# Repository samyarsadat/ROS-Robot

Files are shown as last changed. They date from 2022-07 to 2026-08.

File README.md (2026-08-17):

<h1 align="center">The ROS Robot Project</h1>

<br>

<p align="center">
	
	<br>
	<br>
	
	|
	
	|
	
</p>

<br>

----
> [!NOTE]
> This project was completed and effectively reached its objective in September 2025.\
> There will be no further development. I have moved my focus to the 2nd revision of The ROS Robot.

<br>

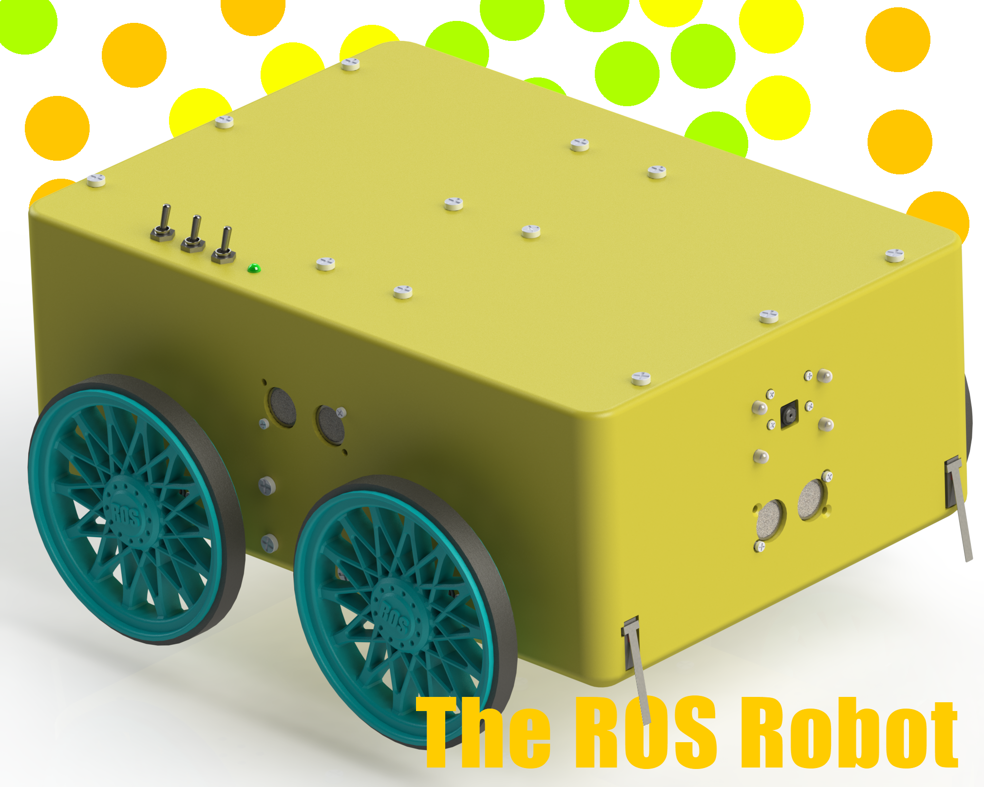
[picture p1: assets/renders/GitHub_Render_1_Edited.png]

This is a 3D render of the CAD drawings.

<br>
<br>

## Overview
### Future Re-design
This is the first revision of the robot. It features a camera for object detection, and a LiDAR sensor for SLAM.

I will begin deisgn work on the second revision/re-design of this robot as soon as this revision is in a state where it can perform mapping and navigation (SLAM), and basic object detection using the camera.

<br>

### System Architecture and Mechanical Design Overview
#### System Architecture
The general architecture of the robot's electronics system consists of a main computer *(the Raspberry Pi 5)* and two, less powerful microcontrollers *(the Raspberry Pi Pico/RP2040)*. The Pi 5 handles image processing, mapping & navigation, and any other type of resource-intensive processing whilst the less-powerful Picos handle I/O for motors, sensors, LEDs, etc.

ROS is used to handle communications between multiple nodes either on the same machine (i.e. a mapping node and a navigation node running on the Pi 5) or between external nodes (i.e. the two Raspberry Pi Picos running microROS). Both Raspberry Pi Picos are connected to the Pi 5 via USB cables.

More details regarding the electronics design [here](electronics/).\
<br>

#### Mechanical Design Overview
The mechanical design of the robot is quite simple. The chassis of the robot is 3D printed in two halves using PLA filament (more details regarding 3D printing [here](cad_files/stl_files/)) and the robot uses four geared DC motors (Namiki 22CL-3501PG) in a differential drive configuration.

<br>

## File Structure
There are 5 folders in this repository.\
Their names and purposes are as follows:

**.github**\
GitHub issue templates, pull request templates, etc.

**assets**\
Assets used on GitHub (such as images used in this README file).

**cad_files**\
3D CAD design files and 3D printing files for the chassis and other mechanical parts of the robot.

**electronics**\
Overall circuit diagrams and PCB design files for the robot.

**source_code**\
Source code for the ROS package of the robot and for the firmware of the Raspberry Pi Picos.

<br>

## Contact
You can contact me via e-mail.\
E-mail: samyarsadat@gigawhat.net\
If you think that you have found a bug or issue please report it <a href="../../issues">here</a>.

<br>

## Contributing
Please take a look at <a href="CONTRIBUTING.md">CONTRIBUTING.md</a> for contributing.

<br>

## Credits
| Role | Name |
| --- | --- |
| Lead Developer | [Samyar Sadat Akhavi](https://github.com/samyarsadat) |
| CAD Design | [Samyar Sadat Akhavi](https://github.com/samyarsadat) |
| PCB Design | [Samyar Sadat Akhavi](https://github.com/samyarsadat) |

<br>

Copyright © 2022-2025 Samyar Sadat Akhavi.

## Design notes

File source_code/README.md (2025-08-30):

## Introduction
This directory contains the source code and related files (such as Dockerfiles for deployment, devconainers for development) for Raspberry Pi Pico firmware and all custom ROS packages that I have written for this project.

<br>

### Operating Systems & Software Versions
**Raspberry Pi OS:** Ubuntu 24.04, Vulcanexus ROS 2 installation. Debian Docker container for RPi AI Kit.\
**Workstation OS:** Ubuntu 24.04, using Docker containers.\
**ROS2 Distribution:** ROS2 Jazzy Jalisco.

<br>

### Directories
 - **pico_ws:** Raspberry Pi Pico workspace. Contains the source code for Raspberry Pi Pico firmware, the source code for the ROS package that contains the custom message definitions that are used by the Picos to communicate with the main Raspberry Pi computer, and a devcontainer for building the firmware and the ROS package. It also contains pre-built binaries for the Picos.
 - **ros_ws_robot_infra:** Robot infrastructure ROS workspace. Contains the source code for all of the base ROS packages that run on the robot (i.e. the driver, the camera image publisher, robot description, LiDAR, etc.), a devcontainer for developing and building the packages, and a Dockerfile for deploying the packages to the robot.
 - **ros_ws_navigation:** Robot navigation ROS workspace. All navigation (nav2) and SLAM related packages and configuration files are here.
 - **ros_camera_ws:** This workspace is for buildind the `camera_ros` package with Raspberry Pi's fork of the `libcamera` library.

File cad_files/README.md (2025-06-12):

## CAD Files

### .SLDPRT & .SLDASM
These files are for people that have access to Solidworks.\
These files are ideal for editing.

<br>

### .STEP
These are editable files that can be opened with almost any CAD software.\
These are for people that want to edit the project but don't have Solidworks.

<br>

### .STL
These are non-editable files used for 3D printing.\
They can be easily imported into all 3D printer slicer software.

<br>

### Robot Description
The `robot_description` directory contains 3D model files prepared for use with ROS.\
They are used for robot visualizations when using RViz or for simulations with Gazebo.

<br>

## Improvements for Re-design
 - **1.**&nbsp; *Add a hole to the back half of the mid plate for wire passthrough.*
 - **2.**&nbsp; *Add two indents to the sides of the mid plate so that it can be removed without having to remove the side ultrasonics.*
 - **3.**&nbsp; *Reinforce motor mounts. (Not necessary. However, it might be beneficial when more weight is added to the robot.)*
 - **4.**&nbsp; *Add cable channels (or holes for zip ties) for better cable management and to prevent too much stress from being put on solder joints/connectors.*
 - **5.**&nbsp; ~~*Remove the need for motor shaft attachments by integrating them into the design of the wheels. (Might be implemented earlier)*~~
 - **6.**&nbsp; *Add indents to the bottom of the robot for IR edge fall-off sensor mounting.*
 - **7.**&nbsp; *Add accommodation for mounting lights to the bottom of the robot.*
 - **8.**&nbsp; *Increase hole tolerances.*
 - **9.**&nbsp; *Add proper mounting holes for voltage regulators and main control board PCB.*
 - **10.**&nbsp; *Fix motor driver mounting hole spacing.*
 - **11.**&nbsp; *Add mounting for the battery.*
 - **12.**&nbsp; *Add holes to the side of the robot to expose the Raspberry Pi's I/O ports.*
 - **13.**&nbsp; *Add mounting for a screen. (Potentially)*
 - **14.**&nbsp; *Add mounting for a cooling fan in the electronics (top) bay.*
 - **15.**&nbsp; *Add a hole for the resettable fuse(s).*
 - **16.**&nbsp; *Change camera mounting to fit the Raspberry Pi Camera Module 3.*
 - **17.**&nbsp; *Add small vent holes around the robot.*
 - **18.**&nbsp; *Add mounting in the front for an 8-led SK6812 module.*

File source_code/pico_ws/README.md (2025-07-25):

## How To Build MicroROS
Run `bash ~/pico_ws/libmicroros/build_uros.sh -rf` as `nonroot` inside of the devcontainer to build the MicroROS library.

<br>

## Pico Firmware Pre-built Binaries
Please take a look at the [`pico-build` workflow](https://github.com/samyarsadat/ROS-Robot/actions/workflows/pico-build.yml) artifact called `pico_binary_artifacts` for the latest binary builds.

#### Action Status
\


<br>
<br>

**NOTE: This devcontainer and the following instructions are written with the assumption that the host machine running Docker runs Linux (specifically, Ubuntu)! If you're using Windows (and can't dualboot Linux), please use the Windows Subsystem for Linux (WSL) to run Docker.**

## Note On Devcontainer
When re-building the devcontainer, the re-build might fail the first time.\
In this case, simply retry the build a second time.

You might have to wait (even after the devcontainer has started) for the MicroROS tools to install.\
Reload the devcontainer after you have verified that the MicroROS tools have installed successfully.\
(Check whether `~/pico_ws/libmicroros/src/micro_ros_setup/install` exists.)

When prompted to select a build kit by the CMake Tools extension, select `GCC [version] arm-none-eabi`.

<br>

## Note On Using Debug Probes
If you're using a debug probe (such as the Raspberry Pi Debug Probe), make sure to create a file named `60-openocd.rules` in `/etc/udev/rules.d` on the host machine (not the devcontainer) and copy the contents of [this file](https://github.com/raspberrypi/openocd/blob/sdk-2.0.0/contrib/60-openocd.rules) into it. This is so that the probe can be accessed witout having to use `sudo`, which is needed when using the Cortex-Debug extension in VSCode.

Run `udevadm control --reload` (again, on the host machine) to make sure that the new rules take effect.

<br>

## Note On GUI Apps & Non-NVIDIA GPUs
If you're using an NVIDIA GPU, make sure to install the NVIDIA Container Toolkit (https://docs.nvidia.com/datacenter/cloud-native/container-toolkit/latest/install-guide.html). If you aren't using an NVIDIA GPU, please remove the `"--gpus", "all",` line from `"runArgs"` in `devcontainer.json`.

For GUI support, the devcontainer is currently configured for using X11. If you're using Wayland, you will have to change the `"-v", "/tmp/.X11-unix:/tmp/.X11-unix:rw",` line from `"runArgs"` in `devcontainer.json`. If you don't want GUI support at all, simply remove `"-v", "/tmp/.X11-unix:/tmp/.X11-unix:rw",` and `"--env=DISPLAY",`.

<br>

### Updating MicroROS Tools or the FreeRTOS Kernel
Discard all changes to the submodule repository, pull the latest version, and rebuild the devcontainer.

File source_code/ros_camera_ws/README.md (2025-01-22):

## Building `camera_ros`
The `ros_ws_robot_infra` setup script ([`source_code/ros_ws_robot_infra/deployment/setup_robot.sh`](../ros_ws_robot_infra/deployment/setup_robot.bash)) 
will take care of building the `camera_ros` package, but in case you want to build it manually yourself:<br>
<br>
Fisrt run the `build_setup_camera_ros.sh` script and then the `build_camera_ros.sh` script, either on the
Raspberry Pi (Ubuntu 24.04, with ROS installed) or inside the `ros_ws_robot_infra` devcontainer.<br>
<br>
These scripts assume that ROS 2 Jazzy Jalisco has already been installed on the system.

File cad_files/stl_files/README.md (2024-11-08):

### 3D Printing details:
   - `Main_Body`, `Top_Plate`, and `Mid_Plate` are designed to be split in half so that they can be printed on smaller printers.
   - You can find already split, ready to print `STL` files in the `ready_to_print` folder.
   - I recommend PLA filament, with 0.28mm layer height, and about 30% infill.
   - `Tire.stl` should be printed with flexible TPU (95A) filament at 0.28mm layer height, and with 10% infill.

<br>

#### Quantities:
    - 1X Main_Body_Center_Support_Plate.stl
    - 2X Main_Body_Side_Support_Plate.stl
    - 1X ready_to_print/Main_Body_Front.stl
    - 1X ready_to_print/Main_Body_Back.stl
    - 1X ready_to_print/Mid_Plate_Front.stl
    - 1X ready_to_print/Mid_Plate_Back.stl
    - 1X Top_Plate_Center_Support_Plate.stl
    - 1X ready_to_print/Top_Plate_Front.stl
    - 1X ready_to_print/Top_Plate_Back.stl
    - 1X Back_Screw_Cover.stl
    - 4X Wheel_V2.stl or Wheel_V2_Flat.stl
    - 4X Tire.stl

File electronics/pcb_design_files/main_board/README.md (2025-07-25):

## Known Issue #1:
*Due to a small design error, plugging in a normal USB cable into the Raspberry Pi Picos will back feed `5v` into the `3.3v` line of the board, potentially damaging some components.*

**Solutions:**<br>
 - **1. Option:**&nbsp; *Modify a normal USB cable by cutting its red (`VCC`) wire, turning it into a data-only cable.*
 - **2. Option:**&nbsp; *Purchase and use a data-only USB cable.*

<br>

## Known Issue #2:
*For unknown reasons, early Raspberry Pi Pico boards (The ones which have an `RP2-B1` marking on their chip) do not work (Windows doesn't recognize the board) when powered only through their `VSYS` pin. So make sure that the Picos that you are going to be using have an `RP2-B2` (or higher) marking on their chips. Changes were made to the USB hardware of the `RP2-B2` (3rd revision) chips however, I am not sure these changes affect this particular issue. I was not able to find any information to suggest that there has been more than one revision of the Raspberry Pi Pico PCB and I also was not able to spot any visual differences between the two boards, so the USB hardware changes to the RP2040 chip itself are probably what fixed this issue but, I am not sure.*

**Solutions:**<br>
 - **1. Option:**&nbsp; *Use Raspberry Pi Pico boards with chips that have `RP2-B2` (or higher) markings on them.*

<br>

## Important Note #1:
*Because this revision of the PCB does not include a voltage divider for measuring the battery voltage, I have attached a wire to pin `ADC2` of Raspberry Pi Pico (B) and created a small protoboard with two resistors on it so that I can measure the voltage of the battery safely. This functionality will be incorporated onto the board itself for rev. 2.*

## Important Note #2:
*On this revision of the PCB, there are two five-pin connectors for the motor encoders. I had initially planned to have one common current limiting resistor for all the encoders, however, this did not work. As a result, I have added a small proto board that splits the two five-pin connectors into four four-pin connectors (one connector per encoder) and adds individual 120ohm current limiting resistors for each encoder. These extra resistors and the four-pin connectors will be incorporated onto the board itself for rev. 2.*

## Important Note #3:
*On this revision of the PCB, all `5V` ultrasonic sensors connect to Pico A through a multiplexer. As a result of this design decision, we cannot use hardware interrupts
when taking measurements. This means that the processor has to wait (after sending a trigger pulse) until either A) a signal is received from the sensor; or B) until a 24ms
timeout is reached. To prevent RTOS task switching during this period (task switching causes unstable readings due to timing variations), a critical section is entered. 
Entering a critical section in FreeRTOS results in all other tasks temporarily entering a suspended state (until the critical section is "exitted" from), even those 
running on the other core of the Pico. This process is repeated for all four ultrasonic sensors (although the front ultrasonic can be optimized to use hardware interrupts 
as its signal pin does not go through the multiplexer) every 200 milliseconds. Given that Pico A also handles motor control and odometry (which are highly time-sensetive
tasks), I have decided to attach all four ultrasonic sensors as well as (potentially) the IMU and magnetometer to a third Raspberry Pi Pico (Pico C).*<br>
<br>
*More details regarding Pico C and its wiring diagram etc. will be added later, as I have not yet connected it.*

<br>

## Board Modification #1:
*The `VCC` pin of the motor encoder connector (`H24`, pin 1) has been rewired to `+5V` (no inline resistors) instead of `+3v3`. <br>
This has been done to improve encoder signal strength.*

## Board Modification #2:
*The `SDA` and `SCL` pins of the `MPU6050` have been rewired to `GP14` and `GP15` respectively (Pico A). <br>
This is so that `GP17` and `GP16` can be used as UART pins for debugging. <br>
For Pico B, `GP8` and `GP9` can be used for UART, as they are already free.*

<br>
<br>

## Improvements for Rev. 2:
 - **1.**&nbsp; *Add diode (or `P-FET`) to Raspberry Pi Pico `VSYS` for power ORing. (https://datasheets.raspberrypi.com/pico/pico-datasheet.pdf)*
 - **2.**&nbsp; *Combine power pins of the IR edge sensors to reduce wire count.*
 - **3.**&nbsp; *Add mounting supports for the `MPU6050` module.*
 - **4.**&nbsp; *Re-position decoupling capacitors to more optimal locations.*
 - **5.**&nbsp; *Add expansion connector that exposes unused ADC pins.*
 - **6.**&nbsp; *Connect fourth, 4-pin ultrasonic connector directly to mux so that it can be used as general analog I/O.*
 - **7.**&nbsp; *Consistent connector pinouts.*
 - **8.**&nbsp; *Replace power input terminal footprint with a 3-pin Molex KK-254 connector.*
 - **9.**&nbsp; *Add battery voltage, current, and temperature monitoring.*
 - **10.**&nbsp; *Add Mosfet for fan control.*
 - **11.**&nbsp; *Add 3-pin addressable LED connectors.*
 - **12.**&nbsp; *Change encoder connectors from two five-pins to four four-pins (individual connector for each encoder).*
 - **13.**&nbsp; *Add individual current limiting resistors and connectors for motor encoders.*
 - **14.**&nbsp; *Motor encoder IR transmitter current limiting resistors should be connected to `5v` instead of `3.3v`.*
 - **15.**&nbsp; *Consider connecting motor encoder pull-up resistors to `5v` instead of `3.3v` or increasing their resistance.*
 - **16.**&nbsp; *Expose one set of `UART` pins of each Pico for debugging.*

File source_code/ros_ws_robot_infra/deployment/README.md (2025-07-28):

These scripts are for setting up, running, and updating all the ROS packages that will run on the robot's on-board Raspberry Pi. I'm using a Raspberry Pi 5 8GB with the Raspberry Pi AI Kit and the Raspberry Pi Camera V3. I'm also running Raspberry Pi OS on the Pi.<br>

You should first run the setup script, then you can make the `run_infra.bash` script execute on startup using `systemd` or GNOME's "Startup Applications" app.

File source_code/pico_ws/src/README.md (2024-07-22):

# Raspberry Pi Pico Source Code
This folder contains the source code (firmware) for the two Raspberry Pi Picos that are on the robot's main board.<br>
The firmware is written in C++ and uses the micro-ROS library to handle communications.<br>
Pre-built binaries can be found in the `build` directory.<br>
<br>

## Important Note #1:
_The motor encoder implementation may look unconventional compared to other robots.<br>
Two different methods are utilized when measuring motor speed:<br>_
<br>

#### First Method
_This method measures the time between each encoder pulse to determine the RPM.<br>
The problem with this method is that when the motor stops, so do RPM calculations (I explain why this is a problem below).
This is because the variables that contain the time at which the last and current pulses were received are only updated when a pulse is received from the encoder (they can **only** be updated when an encoder pulse is received).<br>
<br>
This method produces very accurate and stable RPM readings even with a low-resolution encoder (such as the ones found on the Namiki 22CL-3501PG motors that only send 160 pulses per gearbox shaft rotation);<br>
**However, since RPM calculations stop when the encoders stop sending pulses, RPM readings get stuck at a low value (5~18) even though the motor isn't rotating.**<br>
<br>_

#### Second Method
_This method measures the number of pulses received within a pre-set time period (referred to as the sample time) and then divides 
the number of pulses received by the sample time to get the (average) time between each encoder pulse.<br>
The problem with this method is that its measurements can be a bit choppy/inaccurate/unstable with low-resolution encoders.
This is because there might not be enough pulses sent by the encoder during a single sample period to obtain an accurate RPM reading.<br>
<br>
**Unlike the first method, however, this method can measure 0 RPM without any issues as its RPM calculations do not rely on encoder pulses and are performed on a fixed timer.**<br>
So if no pulses are received during a sample period, the measured RPM will drop to zero, or at least very close to zero (we can round to zero as it will never go down to absolute zero)._<br>
<br>

#### Implementation
_Usually, I would only use the second method for measuring motor speed; However, because the Namiki 22CL-3501PG motors that I'm using have low-resolution encoders, I cannot reliably
and accurately measure motor speeds by only using the second method.<br>
<br>
In the current implementation, motor speed is measured using the first method as long as the speed measured by the second method is above 10 RPM. When the second method's reading drops below 10 RPM,
the program starts using the second method's measurement. Thanks to this implementation, we get accurate readings whilst also being able to measure 0 RPM._<br>

<br>

## Important Note 2:
_This table shows the actual pin numbers to which each motor encoder, driver channel, and microswitch are connected to.<br>
These may not be the same as the ones that are indicated in the Overall Circuit Diagram or the PCB schematics._<br>
<br>

#### Motor Encoders (Pico A)
| Name (definition) | Encoder location | Pico GPIO number | PCB connector |
| --- | --- | --- | --- |
| r_motor_1_enc_a | Front Right (Ch. A) | GPIO 7 | H19 (Pin 5) |
| r_motor_1_enc_b | Front Right (Ch. B) | GPIO 8 | H19 (Pin 4) |
| r_motor_2_enc_a | Back Right (Ch. A) | GPIO 22 | H19 (Pin 1) |
| r_motor_2_enc_b | Back Right (Ch. B) | GPIO 11 | H24 (Pin 5) |
| l_motor_1_enc_a | Front Left (Ch. A) | GPIO 12 | H24 (Pin 3) |
| l_motor_1_enc_b | Front Left (Ch. B) | GPIO 27 | H24 (Pin 4) |
| l_motor_2_enc_a | Back Left (Ch. A) | GPIO 10 | H19 (Pin 2) |
| l_motor_2_enc_b | Back Left (Ch. B) | GPIO 9 | H19 (Pin 3) |
<br>

#### Motor Driver (Pico A)
| Name (definition) | Driver Channel | Pico GPIO number | PCB connector |
| --- | --- | --- | --- |
| r_motor_drive_1 | Out 3 (Right Motors)  | GPIO 20 | H2 (Pin 3) |
| r_motor_drive_2 | Out 4 (Right Motors)  | GPIO 21 | H2 (Pin 2) |
| l_motor_drive_1 | Out 1 (Left Motors) | GPIO 18 | H2 (Pin 5) |
| l_motor_drive_2 | Out 2 (Left Motors) | GPIO 19 | H2 (Pin 4) |
<br>

#### Microswitches (Pico B)
| Name (definition) | Location | Pico GPIO number | PCB connector |
| --- | --- | --- | --- |
| ms_front_r | Front Right  | GPIO 10 | H1 |
| ms_front_l | Front Left | GPIO 11 | H4 |
| ms_back_r | Back Right | GPIO 13 | H11 |
| ms_back_l | Back Left | GPIO 12 | H8 |

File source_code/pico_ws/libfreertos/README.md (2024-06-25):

## Note
`FreeRTOS + POSIX` is no longer used as MicroROS only needs two POSIX functions, and it's much more efficient
just to implement those manually elsewhere. I'm still going to leave the config file for `FreeRTOS + POSIX`
in case it is needed down the road, even though I doubt it will.

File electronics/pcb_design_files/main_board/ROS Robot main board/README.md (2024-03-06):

## File Info:

### .PcbDoc & .SchDoc & .PrjPcb:
These files are for people that have access to Altium Designer.<br>
These files are ideal for editing.<br>

<br>

### Gerber Files:
These are manufacturing files.<br>
They were prepared according to JLCPCB's requirements.<br>
If you are using another manufacturer, you might need to re-export them from Altium according to your manufacturer's requirements.<br>

<br>
<br>

## PCB Connector Info:

#### 5 Volt, 4 pin (Echo, Trigger) ultrasonic sensors:
    Pinout: 
    1: +5v 
    2: GND 
    3: Trigger 
    4: Echo
    
    - H12 (Ultrasonic 1)
    - H13 (Ultrasonic 2)
    - H15 (Ultrasonic 3)
    - H16 (Ultrasonic 4)

#### 3.3 Volt, 3 pin (Echo, Trigger combined) ultrasonic sensor:
    Pinout: 
    1: +3v3 
    2: GND 
    3: Signal Pin (Echo + Trigger)

    - H14 (Ultrasonic 5)

#### Microswitches:
    Pinout (Bi-directional connector): 
    1: Signal 
    2: GND
    
    Note: Microswitches will use RPI Pico's internal pull-up resistors.

    - H11 (Back Left)
    - H8 (Back Right)
    - H4 (Front Left)
    - H1 (Front Right)

#### IR edge sensors:
    Pinout: 
    1: GND 
    2: IR Enable 
    3: +3v3 
    4: Analog Input
    
    - H25 (Edge Sensor 4)
    - H22 (Edge Sensor 3)
    - H20 (Edge Sensor 2)
    - H17 (Edge Sensor 1)
    - H26 (Edge Sensor 8)
    - H23 (Edge Sensor 7)
    - H21 (Edge Sensor 6)
    - H18 (Edge Sensor 5)

#### Motor encoders:
    Pinout (H24): 
    1: +3v3 (Rewired to +5v)
    2: GND 
    3: Back Right Encoder Input (Channel A) 
    4: Back Right Encoder Input (Channel B)
    5: Front Right Encoder Input (Channel A)

    Pinout (H19): 
    1: Front Right Encoder Input (Channel B)
    2: Back Left Encoder Input (Channel A) 
    3: Back Left Encoder Input (Channel B) 
    4: Front Left Encoder Input (Channel A)
    5: Front Left Encoder Input (Channel B)
    
    Note: All encoder inputs are pulled-up to 3.3v by 4.7k resistors.

    - H24 (Encoder Connector A)
    - H19 (Encoder Connector B)

#### Camera LEDs:
    Pinout:
    1: GND
    2: Camera LED Output 1
    2: Camera LED Output 2
    2: Camera LED Output 3
    2: Camera LED Output 4
    
    Note: All camera LED outputs are directly connected to RPI Pico's GPIOs without current limiting resistors.

    - H9

#### Motor driver:
    Pinout:
    1: GND
    2: Left Motor Output (Channel B)
    3: Left Motor Output (Channel A)
    4: Right Motor Output (Channel B)
    5: Right Motor Output (Channel A)

    - H2

#### Raspberry Pi 4 power relay:
    Pinout:
    1: Signal Output
    2: VCC (Can be set to +3v3 or +5v via a jumper (J1))
    3: GND

    - H6

#### Front panel:
    Pinout:
    1: Speed Select Switch Input (Contact 1)
    2: Mode Select Switch Input
    3: Speed Select Switch Input (Contact 2)
    4: GND
    5: Indicator LED Output (Through a 220ohm resistor)

    - H10
   
<br>
<br>

## Component values:

#### Resistors (All footprints are 1206 SMD):
    R5, R7, R8, R10, R11, R12, R13, R16 = 4.7k
    R1, R3, R4, R6 = 220ohm
    R2 = 430ohm
    R9 = 10k
    R15 = 0ohm (Shorted)
    R14 = Unpopulated
    
#### Capacitors (All footprints are 1206 SMD, Ceramic):
    C1 = 100nf
    C2, C3, C4 = 100nf (Not required)
    
#### Diodes & LEDs (All footprints are 1206 SMD):
    D1 = 1N5822 (or any similar Schottky diode)
    D2 = Red LED (+5v indicator LED)
    D3 = Green LED (+3v3 indicator LED)
    D4 = Blue LED (Edge IR sensor mosfet active indicator LED)

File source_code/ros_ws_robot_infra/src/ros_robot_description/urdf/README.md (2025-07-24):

> [!NOTE]
> URDF files are partially based on [Rosbot robot_description](https://github.com/husarion/rosbot_ros/tree/jazzy/rosbot_description).

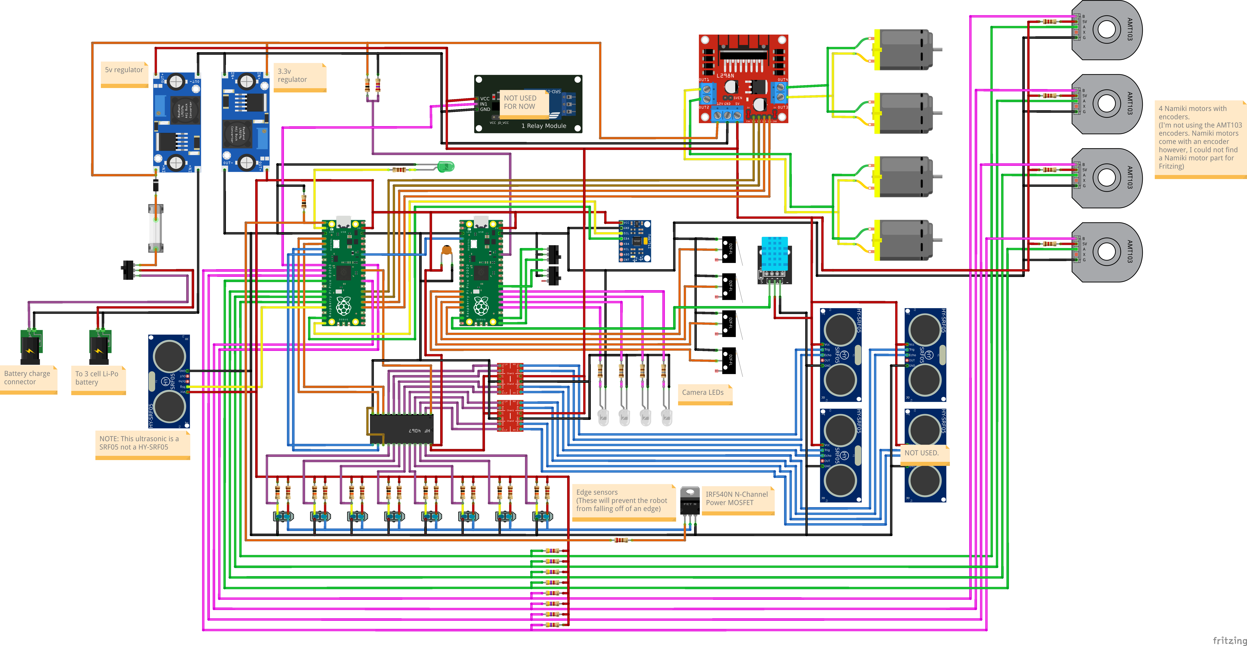
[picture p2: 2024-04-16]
electronics/circuit_diagrams/overall/Circuit_Diagram.png

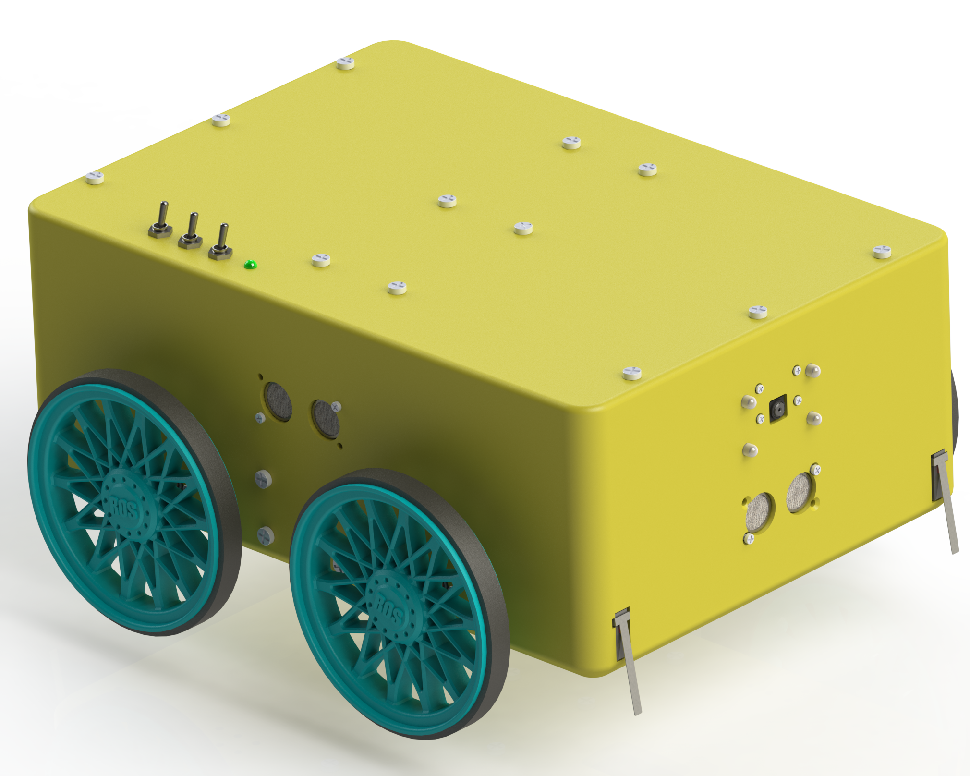
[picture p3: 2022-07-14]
assets/renders/GitHub_Render_1.png

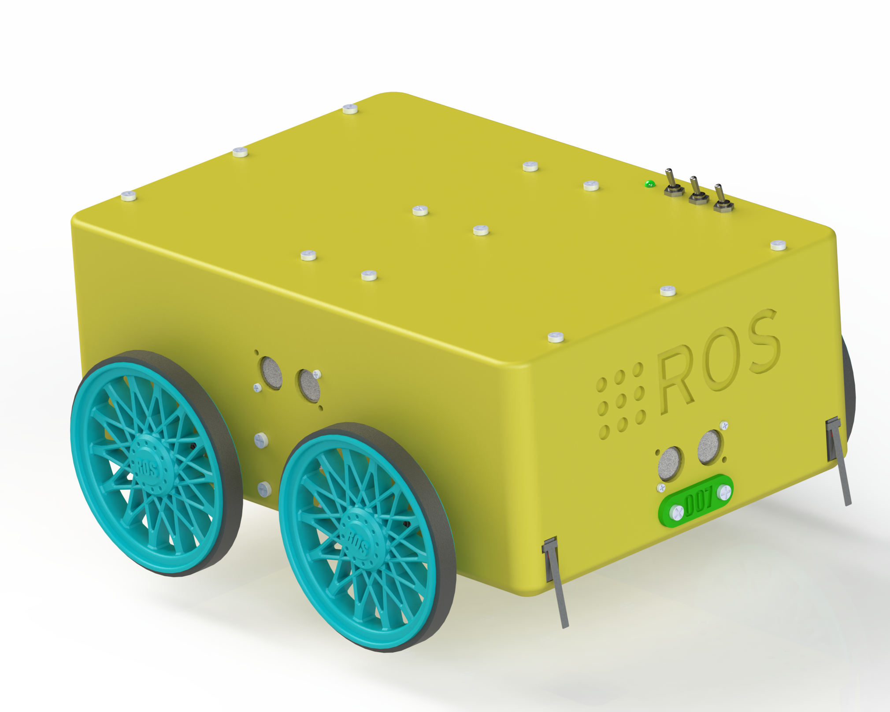
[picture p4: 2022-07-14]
assets/renders/GitHub_Render_2.png

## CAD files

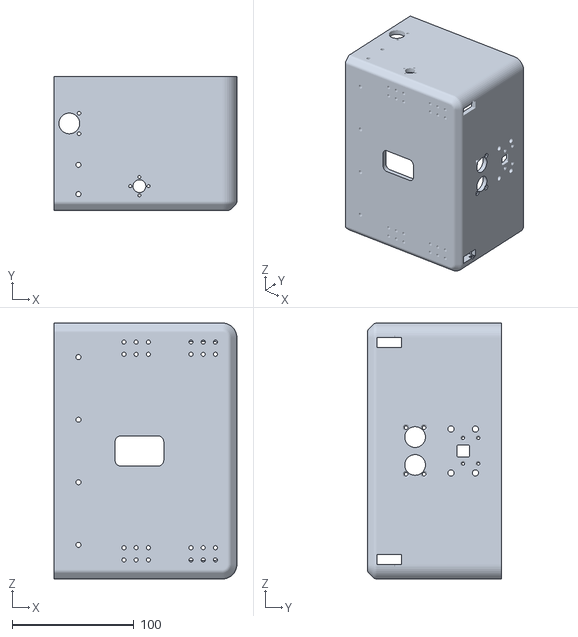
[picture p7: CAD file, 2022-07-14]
cad_files/stl_files/ready_to_print/Main_Body_Front.stl
150.0 x 110.0 x 210.0

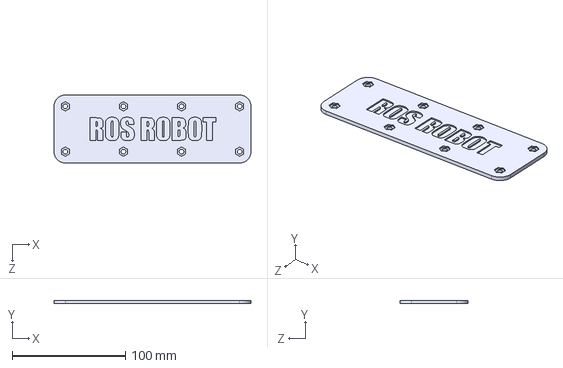
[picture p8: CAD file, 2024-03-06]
cad_files/step_files/Main_Body_Center_Support_Plate.STEP
174.0 x 3.00 x 60.0 mm

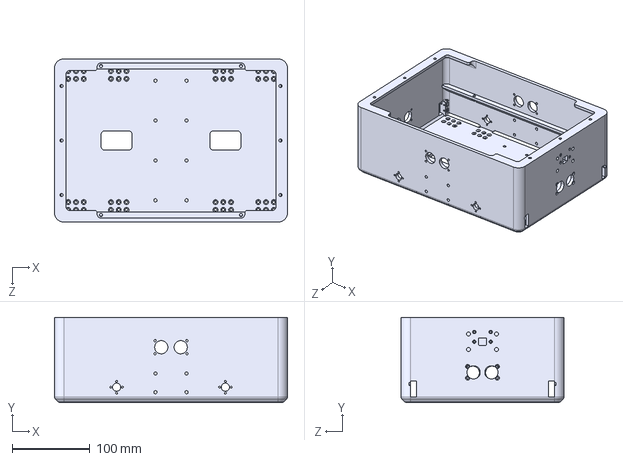
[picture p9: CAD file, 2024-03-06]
cad_files/step_files/Main_Body.STEP
300.0 x 110.0 x 210.0 mm

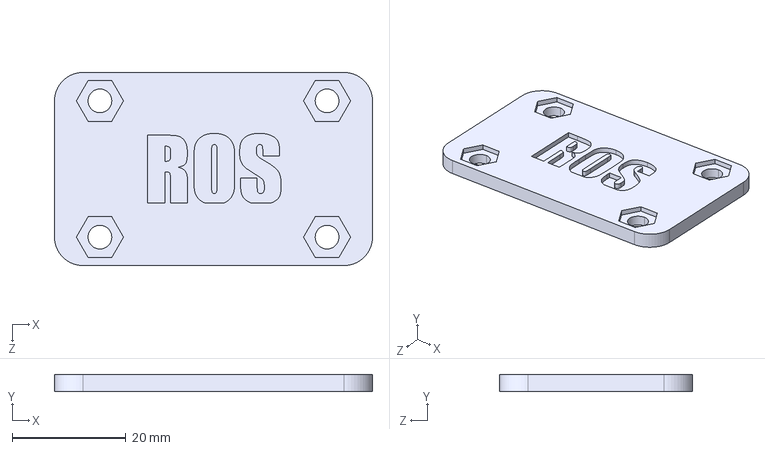
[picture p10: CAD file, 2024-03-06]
cad_files/step_files/Main_Body_Side_Support_Plate.STEP
56.0 x 3.00 x 34.0 mm

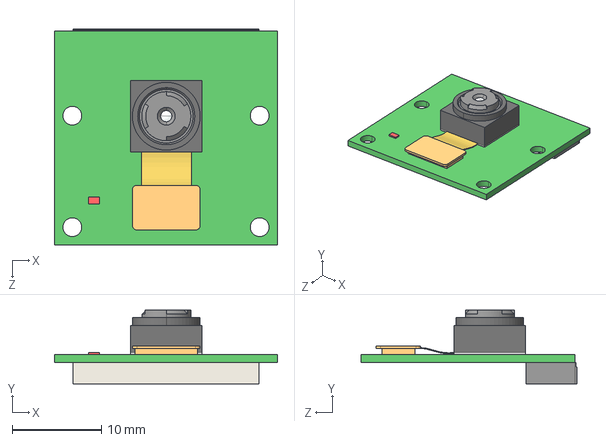
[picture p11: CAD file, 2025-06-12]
cad_files/robot_description/step_interim/rpi_camera.STEP
25.0 x 8.25 x 24.2 mm

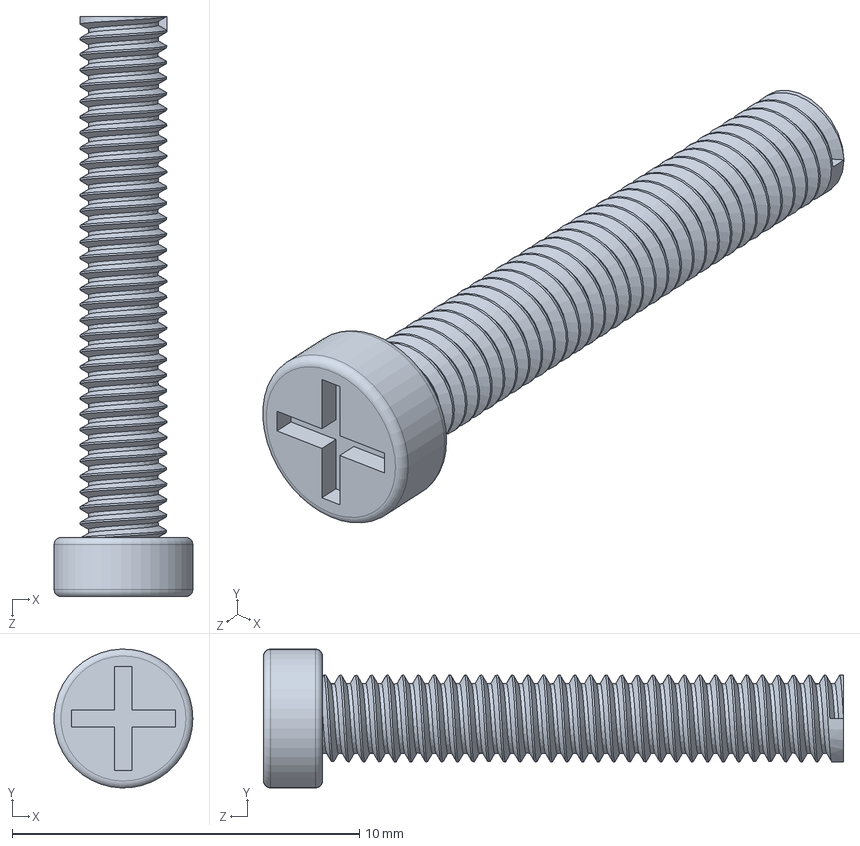
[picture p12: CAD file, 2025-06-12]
cad_files/solidworks_assets/parts/M2.5_15.SLDPRT
3.99 x 4.00 x 16.7 mm

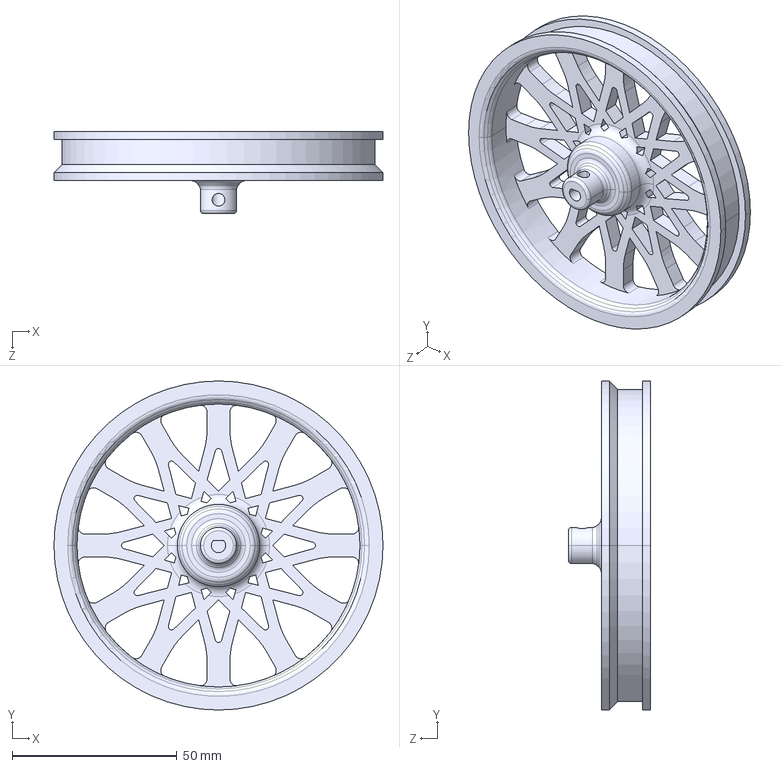
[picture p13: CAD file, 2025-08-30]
cad_files/step_files/Wheel_V2_Flat.STEP
100.0 x 100.0 x 25.0 mm

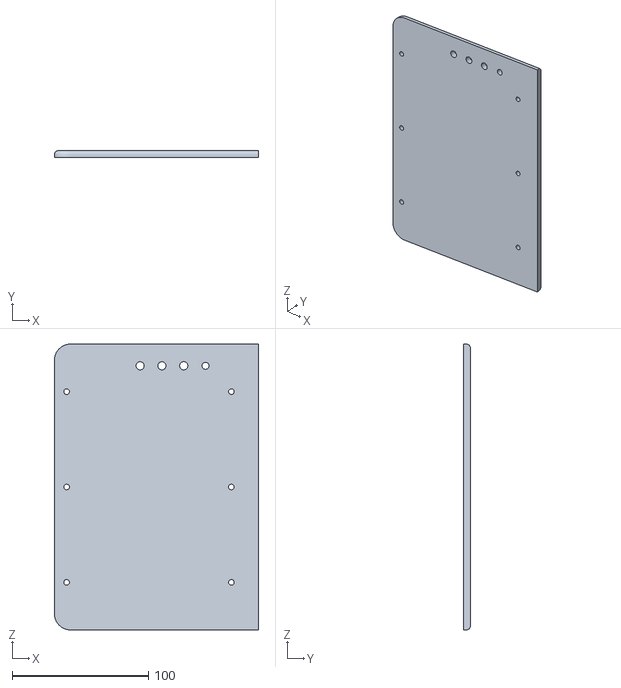
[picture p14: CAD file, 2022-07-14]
cad_files/stl_files/ready_to_print/Top_Plate_Back.stl
150.0 x 5.00 x 210.0

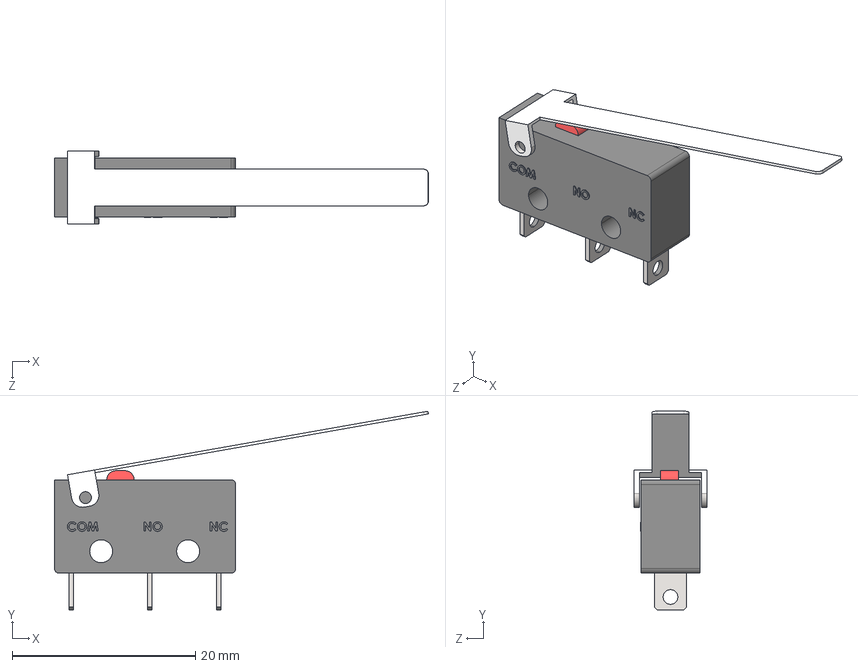
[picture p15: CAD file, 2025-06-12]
cad_files/robot_description/step_interim/micro_switch.STEP
40.9 x 21.7 x 8.00 mm

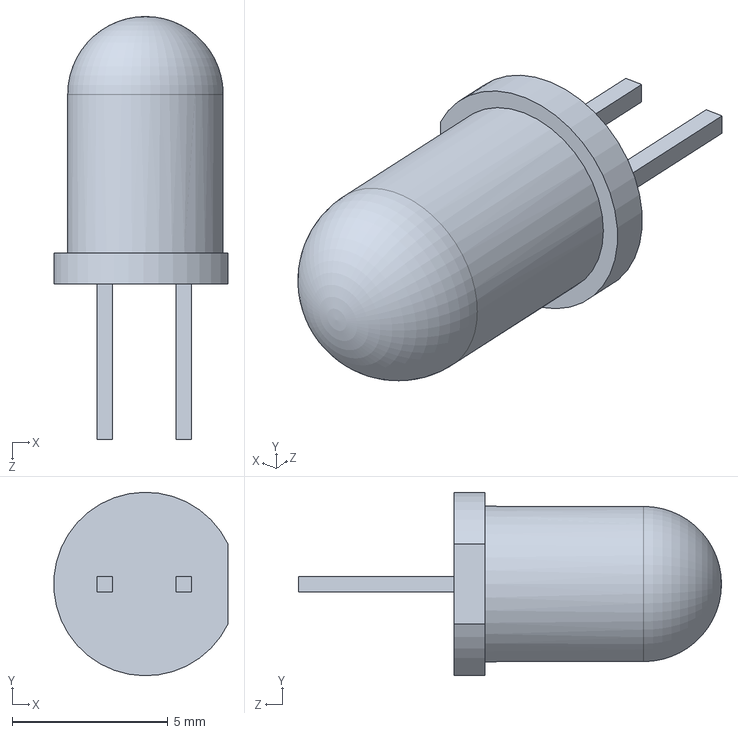
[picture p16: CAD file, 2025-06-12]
cad_files/solidworks_assets/parts/White_led.SLDPRT
5.59 x 5.90 x 13.6 mm

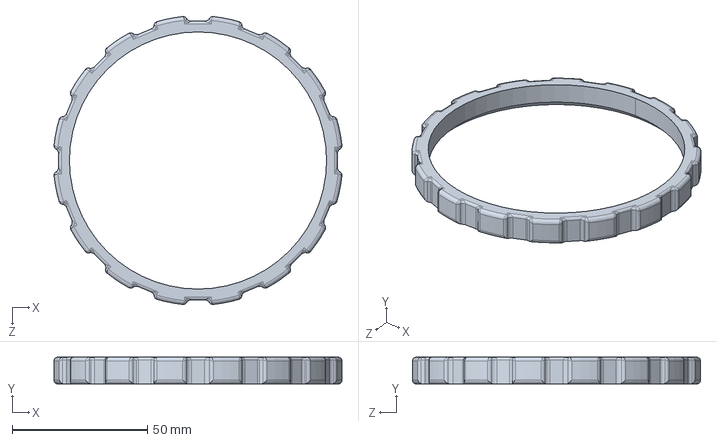
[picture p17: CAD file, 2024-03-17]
cad_files/step_files/Tire.STEP
106.4 x 9.90 x 106.4 mm

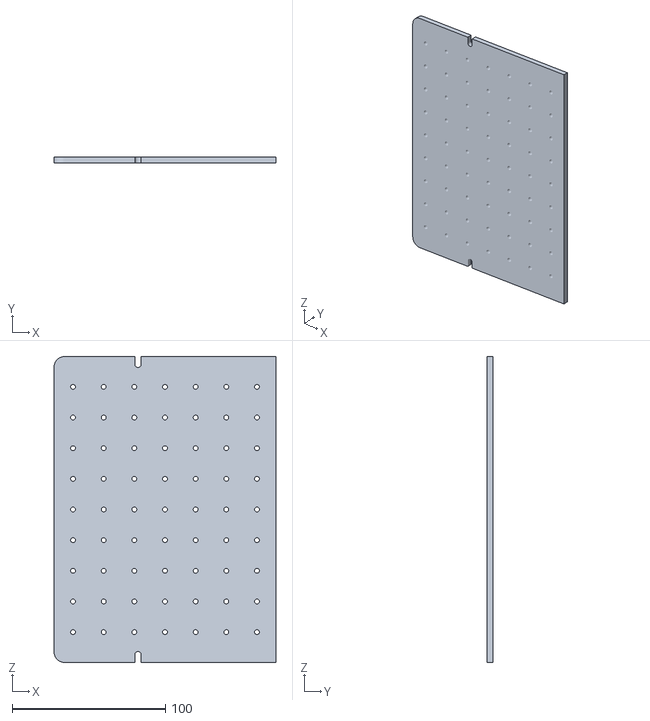
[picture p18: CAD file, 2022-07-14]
cad_files/stl_files/ready_to_print/Mid_Plate_Back.stl
144.8 x 4.00 x 199.6

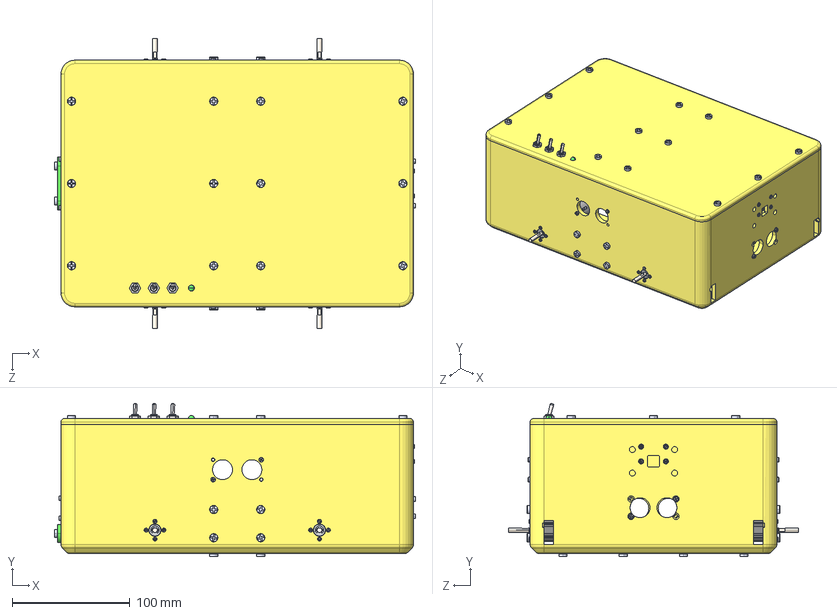
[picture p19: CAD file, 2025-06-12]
cad_files/robot_description/step_interim/body.STEP
307.2 x 130.3 x 246.4 mm
Main_Body
Namiki_with_encoder x 4
M2.5_10 x 8
M2_15 x 16
M2_10 x 4
Top_Plate
M4_15 x 30
Back_Screw_Cover
Toggle_Switch x 3
M6_nut x 3
Green_led

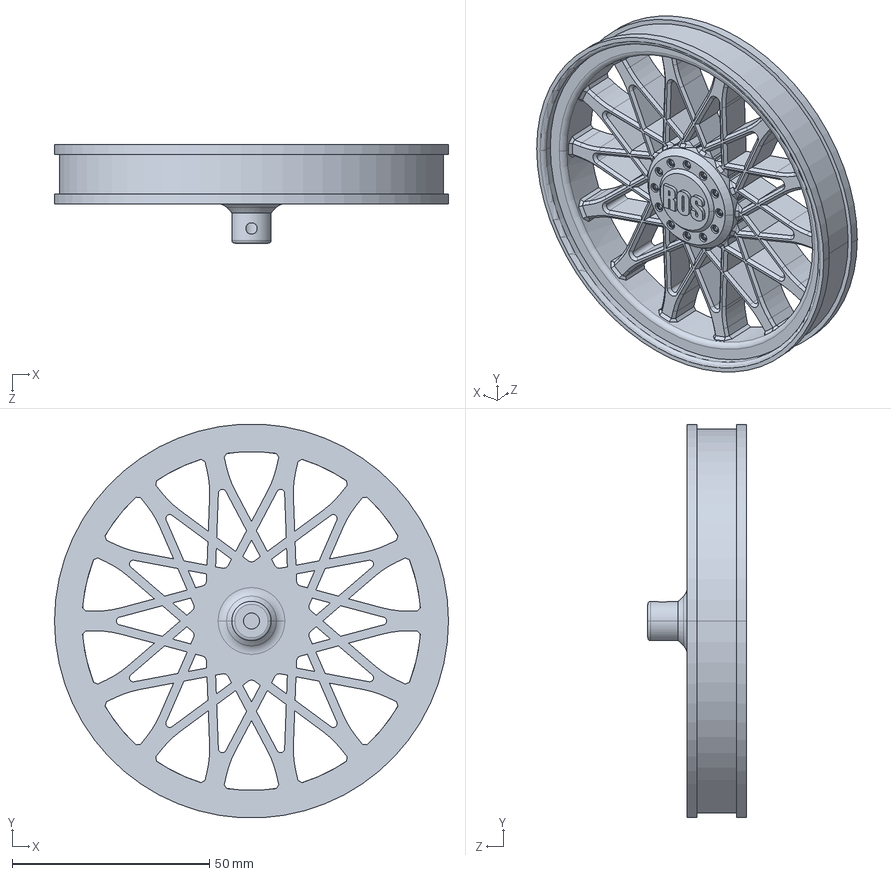
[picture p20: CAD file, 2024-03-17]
cad_files/step_files/Wheel_V2.STEP
100.0 x 99.9 x 25.0 mm

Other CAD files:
cad_files/IR_Cliff_Sensor.SLDASM
cad_files/Assembly.SLDASM
cad_files/Descr_Wheel_Assembly.SLDASM
cad_files/stl_files/ready_to_print/Main_Body_Back.stl
cad_files/Back_Screw_Cover.SLDPRT
cad_files/Main_Body.SLDPRT
cad_files/Main_Body_Center_Support_Plate.SLDPRT
cad_files/Main_Body_Side_Support_Plate.SLDPRT
cad_files/Mid_Plate.SLDPRT
cad_files/Tire.SLDPRT
cad_files/Top_Plate.SLDPRT
cad_files/Top_Plate_Center_Support_Plate.SLDPRT
cad_files/Wheel.SLDPRT
cad_files/Wheel_V2.SLDPRT
cad_files/Wheel_V2_Flat.SLDPRT
cad_files/robot_description/blend_interim/camera_led.blend
cad_files/robot_description/blend_interim/ir_cliff_sensor.blend
cad_files/robot_description/blend_interim/micro_switch.blend
cad_files/robot_description/blend_interim/rpi_camera.blend
cad_files/robot_description/blend_interim/ultrasonic_hysrf05.blend
cad_files/robot_description/blend_interim/ultrasonic_srf05.blend
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

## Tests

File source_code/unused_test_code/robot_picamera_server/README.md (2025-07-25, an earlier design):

## Robot PiCamera2 Server
This was a test program written to expose a Raspberry Pi Camera through an HTTP server using PiCamera2 and FastAPI. It is no longer necessary, as I have chosen a different method for getting and publishing images from the Raspberry Pi Camera V3.

The Raspberry Pi Camera V3 only supports the new camera stack, which uses `libcamera`, and it also uses the Sony IMX708 image sensor. The Linux kernel version used by Ubuntu 22.04 does not support the IMX708. This means that it would be highly impractical to attempt to use the camera directly with Ubuntu 22.04. As such, I decided to run Raspberry Pi OS as the host operating system of the robot's on-board Raspberry Pi 5 and to run all ROS-related nodes in Docker containers running Ubuntu 22.04. I would then run this server on the host OS and have a separate node inside of a Docker container, which would then use the HTTP API provided by the server to get images (or a stream of images) from the camera and publish them to ROS topics. This proved highly inefficient, especially for uncompressed image streams. I have decided to publish the code for the server here regardless, hoping that it may be of some use to someone.

As for the robot itself, I have decided to upgrade from ROS 2 Humble Hawksbill to ROS 2 Jazzy Jalisco, the next LTS release of ROS 2, allowing me to use Ubuntu 24.04 instead of 22.04. Ubuntu 24.04 fully supports the IMX708 as well as the new `libcamera`-based camera stack from Raspberry Pi. Granted, this will require numerous changes to Dockerfiles amongst other configuration files, both for the ROS Robot and the ROS Remote. However, I don't see myself as having much of a choice in this matter, I'm afraid.

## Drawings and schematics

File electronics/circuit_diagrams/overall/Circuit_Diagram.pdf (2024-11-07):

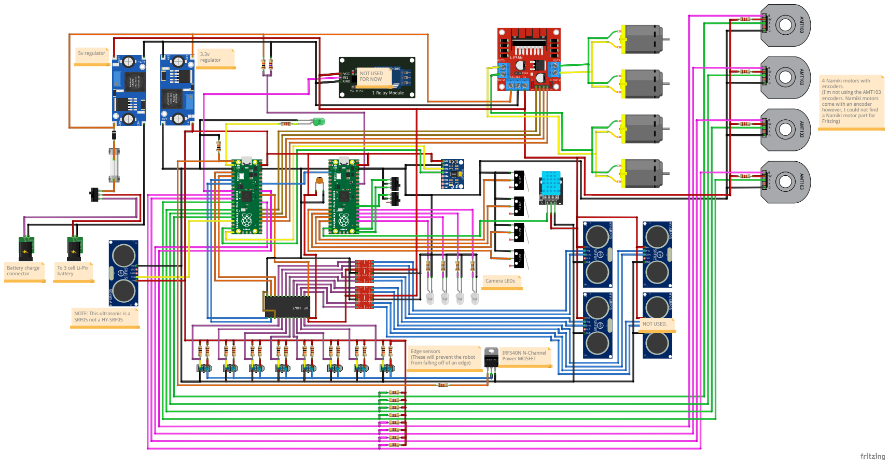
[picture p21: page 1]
Battery charge connector; IRF540N N-Channel Power MOSFET; Camera LEDs; 3.3v regulator; 5v regulator; NOT USED.; NOT USED FOR NOW

4 Namiki motors with
encoders.
(I'm not using the AMT103
encoders. Namiki motors
come with an encoder
however, I could not find
a Namiki motor part for
Fritzing)

To 3 cell Li-Po
battery

NOTE: This ultrasonic is a
SRF05 not a HY-SRF05

Edge sensors
(These will prevent the robot
from falling off of an edge)

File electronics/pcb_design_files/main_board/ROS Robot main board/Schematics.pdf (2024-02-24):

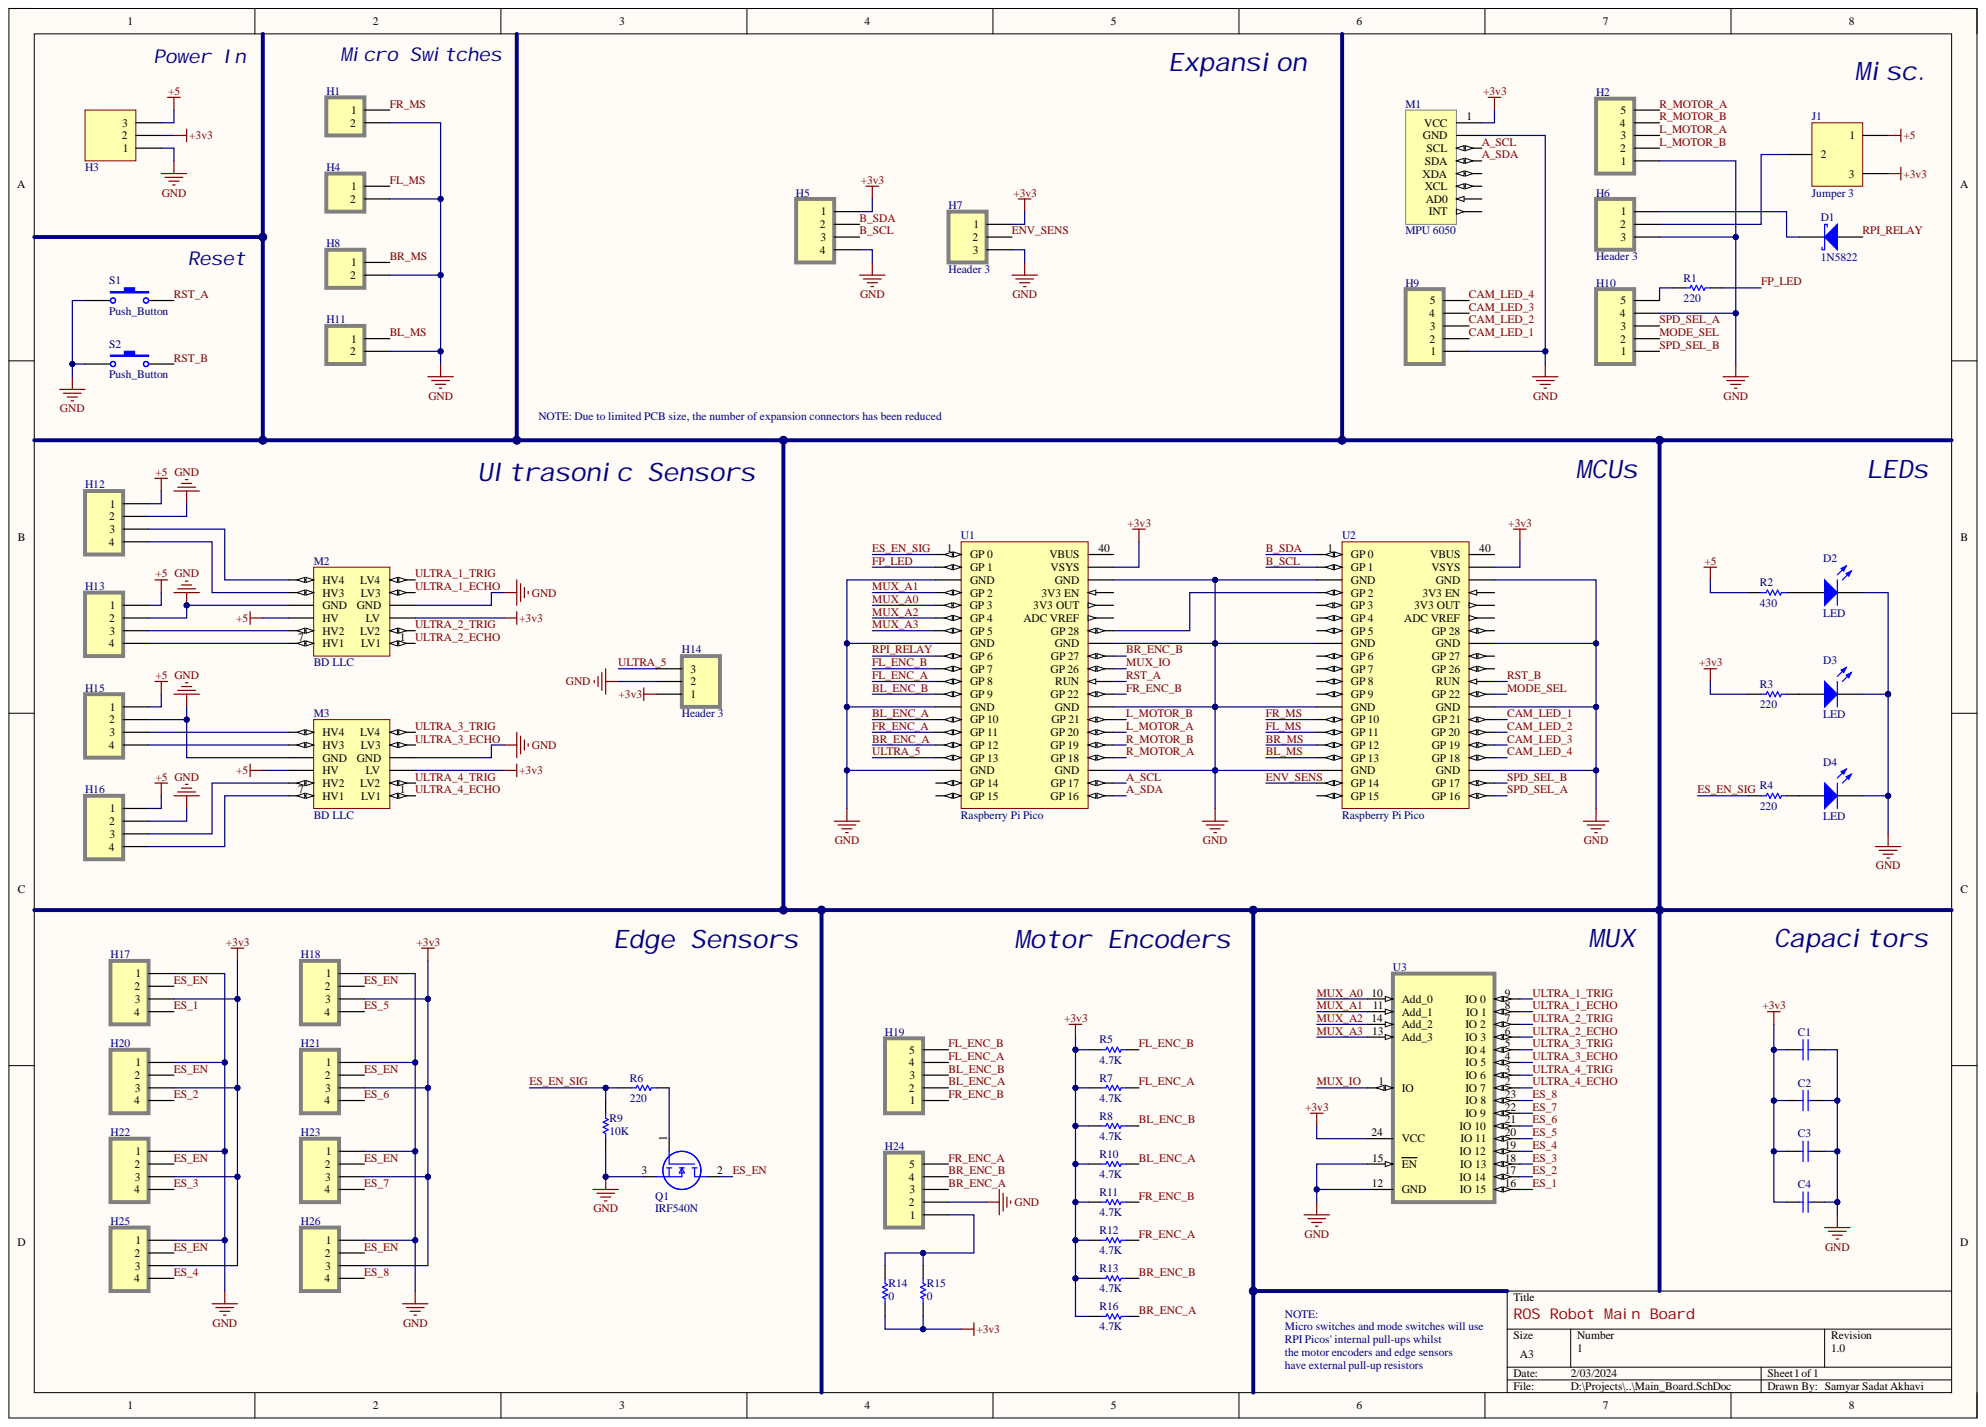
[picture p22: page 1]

NOTE: Due to limited PCB size, the number of expansion connectors has been reduced

Title
ROS Robot Main Board

NOTE:
Micro switches and mode switches will use
RPI Picos' internal pull-ups whilst
the motor encoders and edge sensors
have external pull-up resistors

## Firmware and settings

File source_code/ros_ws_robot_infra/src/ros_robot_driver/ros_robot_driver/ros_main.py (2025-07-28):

#  The ROS robot project (Robot Driver Package)
#  ROS setup, node, and executor
#  Copyright 2024-2025 Samyar Sadat Akhavi
#  Written by Samyar Sadat Akhavi, 2024-2025.
#
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
import array
import sys
import threading
import time
import rclpy
from asyncio import Future
from typing import Union
from rclpy.callback_groups import ReentrantCallbackGroup, MutuallyExclusiveCallbackGroup
from rclpy.client import SrvTypeRequest, Client, SrvTypeResponse
from ros_robot_driver.driver_impl import ros_robot_interface
from rclpy.executors import ExternalShutdownException
from rclpy.executors import MultiThreadedExecutor
from rclpy.node import Node
from ros_robot_driver.config import RosConfig, RosNames
from rrp_pico_coms.msg import MiscSensorsA, UltrasonicSensors, FalloffSensors, MotorCtrlState, FastOdometry, MiscSensorsB, MicroSwSensors
from geometry_msgs.msg import Twist
from rrp_pico_coms.srv import SetPidTunings, SetCameraLeds, RunCalibrationsA, GetConfigA
from std_srvs.srv import SetBool
from std_msgs.msg import Empty
from diagnostic_msgs.srv import SelfTest
from diagnostic_msgs.msg import DiagnosticStatus
from copy import deepcopy


# ---- Global variables ----
_stop_ros_thread = False
_ros_thread = None


# ---- ROS Node ----
class RosNode(Node):
    # Client.call() implementation with timeout.
    def srv_call_with_timeout(self, client: Client, request: SrvTypeRequest, timeout_s: int) -> Union[SrvTypeResponse, None]:
        event = threading.Event()

        def unblock(ftr):
            event.set()

        future = client.call_async(request)
        future.add_done_callback(unblock)

        if not future.done():
            if not event.wait(float(timeout_s)):
                self.get_logger().error(f"Service call failure [{client.srv_name}]: timed out! Cancelling.")
                future.cancel()
                return None

        if future.exception() is not None:
            raise future.exception()

        return future.result()

    def __init__(self, context: rclpy.Context, node_name: str):
        super().__init__(context=context, node_name=node_name)
        self.get_logger().info("Creating publishers, subscribers, and services servers...")

        self._reentrant_cb_group = ReentrantCallbackGroup()
        self._selftest_calib_cb_group = MutuallyExclusiveCallbackGroup()
        self._emer_stop_cb_group = MutuallyExclusiveCallbackGroup()

        self._emergency_stop_pub = self.create_publisher(Empty, RosNames.EMERGENCY_STOP_TOPIC, qos_profile=RosConfig.QOS_RELIABLE, callback_group=self._emer_stop_cb_group)
        self._command_vel_pub = self.create_publisher(Twist, RosNames.COMMAND_VEL_TOPIC, qos_profile=RosConfig.QOS_RELIABLE, callback_group=self._reentrant_cb_group)

        self._diagnostics_sub = self.create_subscription(DiagnosticStatus, RosNames.DIAGNOSTICS_TOPIC, self.diagnostics_call, qos_profile=RosConfig.QOS_BEST_EFFORT, callback_group=self._reentrant_cb_group)
        self._pico_a_misc_sens_sub = self.create_subscription(MiscSensorsA, RosNames.PICO_A_MISC_SENS_TOPIC, self.pico_a_misc_sens_call, qos_profile=RosConfig.QOS_BEST_EFFORT, callback_group=self._reentrant_cb_group)
        self._ultrasonic_sens_sub = self.create_subscription(UltrasonicSensors, RosNames.ULTRASONIC_SENS_TOPIC, self.ultrasonic_sens_call, qos_profile=RosConfig.QOS_BEST_EFFORT, callback_group=self._reentrant_cb_group)
        self._cliff_sens_sub = self.create_subscription(FalloffSensors, RosNames.CLIFF_SENS_TOPIC, self.cliff_sens_call, qos_profile=RosConfig.QOS_BEST_EFFORT, callback_group=self._reentrant_cb_group)
        self._motor_ctrl_state_r_sub = self.create_subscription(MotorCtrlState, RosNames.MOTOR_CTRL_STATE_R_TOPIC, self.motor_ctrl_state_r_call, qos_profile=RosConfig.QOS_BEST_EFFORT, callback_group=self._reentrant_cb_group)
        self._motor_ctrl_state_l_sub = self.create_subscription(MotorCtrlState, RosNames.MOTOR_CTRL_STATE_L_TOPIC, self.motor_ctrl_state_l_call, qos_profile=RosConfig.QOS_BEST_EFFORT, callback_group=self._reentrant_cb_group)
        self._encoder_odom_sub = self.create_subscription(FastOdometry, RosNames.ENC_ODOMETRY_TOPIC, self.encoder_odom_call, qos_profile=RosConfig.QOS_BEST_EFFORT, callback_group=self._reentrant_cb_group)
        self._pico_b_misc_sens_sub = self.create_subscription(MiscSensorsB, RosNames.PICO_B_MISC_SENS_TOPIC, self.pico_b_misc_sens_call, qos_profile=RosConfig.QOS_BEST_EFFORT, callback_group=self._reentrant_cb_group)
        self._micro_sw_sens_sub = self.create_subscription(MicroSwSensors, RosNames.MICRO_SW_SENS_TOPIC, self.micro_sw_sens_call, qos_profile=RosConfig.QOS_BEST_EFFORT, callback_group=self._reentrant_cb_group)

        self._en_motor_ctrl_srvcl = self.create_client(SetBool, RosNames.EN_MOTOR_CTRL_SRV, qos_profile=RosConfig.QOS_RELIABLE)
        self._en_emitters_srvcl = self.create_client(SetBool, RosNames.EN_EMITTERS_SRV, qos_profile=RosConfig.QOS_RELIABLE)
        self._en_relay_srvcl = self.create_client(SetBool, RosNames.EN_RELAY_SRV, qos_profile=RosConfig.QOS_RELIABLE)
        self._set_mtr_pid_tunings_srvcl = self.create_client(SetPidTunings, RosNames.SET_MTR_PID_TUNINGS_SRV, qos_profile=RosConfig.QOS_RELIABLE)
        self._pico_a_run_selftest_srvcl = self.create_client(SelfTest, RosNames.PICO_A_RUN_SELFTEST_SRV, qos_profile=RosConfig.QOS_RELIABLE, callback_group=self._selftest_calib_cb_group)
        self._pico_a_run_calib_srvcl = self.create_client(RunCalibrationsA, RosNames.PICO_A_RUN_CALIB_SRV, qos_profile=RosConfig.QOS_RELIABLE, callback_group=self._selftest_calib_cb_group)
        self._pico_a_get_config_srvcl = self.create_client(GetConfigA, RosNames.PICO_A_GET_CONFIG_SRV, qos_profile=RosConfig.QOS_RELIABLE)
        self._en_camera_leds_srvcl = self.create_client(SetCameraLeds, RosNames.EN_CAMERA_LEDS_SRV, qos_profile=RosConfig.QOS_RELIABLE)
        self._pico_b_run_selftest_srvcl = self.create_client(SelfTest, RosNames.PICO_B_RUN_SELFTEST_SRV, qos_profile=RosConfig.QOS_RELIABLE, callback_group=self._selftest_calib_cb_group)

        self._pico_a_get_config_future = None

        self._en_motor_ctrl_req = SetBool.Request()
        self._en_emitters_req = SetBool.Request()
        self._en_relay_req = SetBool.Request()
        self._set_mtr_pid_tunings_req = SetPidTunings.Request()
        self._pico_a_run_selftest_req = SelfTest.Request()
        self._pico_a_run_calib_req = RunCalibrationsA.Request()
        self._pico_a_get_config_req = GetConfigA.Request()
        self._en_camera_leds_req = SetCameraLeds.Request()
        self._pico_b_run_selftest_req = SelfTest.Request()

    def publish_command_vel(self, linear_vel: float, angular_vel: float) -> None:
        msg = Twist()
        msg.linear.x = linear_vel
        msg.angular.z = angular_vel
        self._command_vel_pub.publish(msg)

    def publish_emergency_stop(self) -> None:
        self.get_logger().warn("Emergency stop received!")
        self._emergency_stop_pub.publish(Empty())

    def en_motor_ctrl(self, enable: bool) -> Union[SetBool.Response, None]:
        if self._en_motor_ctrl_srvcl.service_is_ready():
            self._en_motor_ctrl_req.data = enable
            return self.srv_call_with_timeout(self._en_motor_ctrl_srvcl, self._en_motor_ctrl_req, RosConfig.SERVICE_CALL_TIMEOUT)
        self.get_logger().error(f"Service call failure [{self._en_motor_ctrl_srvcl.srv_name}]: service not ready!")
        return None

    def en_emitters(self, enable: bool) -> Union[SetBool.Response, None]:
        if self._en_emitters_srvcl.service_is_ready():
            self._en_emitters_req.data = enable
            return self.srv_call_with_timeout(self._en_emitters_srvcl, self._en_emitters_req, RosConfig.SERVICE_CALL_TIMEOUT)
        self.get_logger().error(f"Service call failure [{self._en_emitters_srvcl.srv_name}]: service not ready!")
        return None

    def en_relay(self, enable: bool) -> Union[SetBool.Response, None]:
        if self._en_relay_srvcl.service_is_ready():
            self._en_relay_req.data = enable
            return self.srv_call_with_timeout(self._en_relay_srvcl, self._en_relay_req, RosConfig.SERVICE_CALL_TIMEOUT)
        self.get_logger().error(f"Service call failure [{self._en_relay_srvcl.srv_name}]: service not ready!")
        return None

    def set_mtr_pid_tunings(self, kp: float, ki: float, kd: float) -> Union[SetPidTunings.Response, None]:
        if self._set_mtr_pid_tunings_srvcl.service_is_ready():
            self._set_mtr_pid_tunings_req.pid_kp = kp
            self._set_mtr_pid_tunings_req.pid_ki = ki
            self._set_mtr_pid_tunings_req.pid_kd = kd
            return self.srv_call_with_timeout(self._set_mtr_pid_tunings_srvcl, self._set_mtr_pid_tunings_req, RosConfig.SERVICE_CALL_TIMEOUT)
        self.get_logger().error(f"Service call failure [{self._set_mtr_pid_tunings_srvcl.srv_name}]: service not ready!")
        return None

    def run_pico_a_selftest(self) -> Union[SelfTest.Response, None]:
        if self._pico_a_run_selftest_srvcl.service_is_ready():
            return self.srv_call_with_timeout(self._pico_a_run_selftest_srvcl, self._pico_a_run_selftest_req, RosConfig.SERVICE_CALL_TIMEOUT)
        self.get_logger().error(f"Service call failure [{self._pico_a_run_selftest_srvcl.srv_name}]: service not ready!")
        return None

    def run_pico_a_calib(self, calib_ir_cliff: bool, calib_imu: bool, autotune_pid_left: bool, autotune_pid_right: bool) -> Union[RunCalibrationsA.Response, None]:
        if self._pico_a_run_calib_srvcl.service_is_ready():
            self._pico_a_run_calib_req.calib_ir_edge = calib_ir_cliff
            self._pico_a_run_calib_req.calib_imu = calib_imu
            self._pico_a_run_calib_req.calib_pid_left = autotune_pid_left
            self._pico_a_run_calib_req.calib_pid_right = autotune_pid_right
            return self.srv_call_with_timeout(self._pico_a_run_calib_srvcl, self._pico_a_run_calib_req, RosConfig.SERVICE_CALL_TIMEOUT)
        self.get_logger().error(f"Service call failure [{self._pico_a_run_calib_srvcl.srv_name}]: service not ready!")
        return None

    def set_camera_leds(self, led_outputs: array.array) -> Union[SetCameraLeds.Response, None]:
        if self._en_camera_leds_srvcl.service_is_ready():
            self._en_camera_leds_req.led_outputs = led_outputs
            return self.srv_call_with_timeout(self._en_camera_leds_srvcl, self._en_camera_leds_req, RosConfig.SERVICE_CALL_TIMEOUT)
        self.get_logger().error(f"Service call failure [{self._en_camera_leds_srvcl.srv_name}]: service not ready!")
        return None

    def run_pico_b_selftest(self) -> Union[SelfTest.Response, None]:
        if self._pico_b_run_selftest_srvcl.service_is_ready():
            return self.srv_call_with_timeout(self._pico_b_run_selftest_srvcl, self._pico_b_run_selftest_req, RosConfig.SERVICE_CALL_TIMEOUT)
        self.get_logger().error(f"Service call failure [{self._pico_b_run_selftest_srvcl.srv_name}]: service not ready!")
        return None

    def init_config_vars(self) -> bool:
        if self._pico_a_get_config_srvcl.service_is_ready():
            self._pico_a_get_config_future = self._pico_a_get_config_srvcl.call_async(self._pico_a_get_config_req)
            self._pico_a_get_config_future.add_done_callback(self._init_config_vars_future_call)
            return True
        self.get_logger().error(f"Service call failure [{self._pico_a_get_config_srvcl.srv_name}]: service not ready!")
        return False

    def _init_config_vars_future_call(self, future: Future):
        response = future.result()

        if response:
            ros_robot_interface.motor_wheel_info._encoder_ppr = response.encoder_pulses_per_rotation
            ros_robot_interface.motor_wheel_info._wheelbase_mm = response.wheelbase_mm
            ros_robot_interface.motor_wheel_info._wheel_diameter_mm = response.wheel_diameter_mm
            ros_robot_interface.motor_wheel_info._motor_gear_ratio = response.motor_gear_ratio_fl
            ros_robot_interface.right_motor_controller._pid_tunings = array.array("f", response.pid_cals_right)
            ros_robot_interface.left_motor_controller._pid_tunings = array.array("f", response.pid_cals_left)

            for i in range(0, 4):
                ros_robot_interface.ultrasonic_sensors[i]._field_of_view = response.ultrasonic_fov
                ros_robot_interface.ultrasonic_sensors[i]._min_distance = float(response.ultrasonic_min_dist)
                ros_robot_interface.ultrasonic_sensors[i]._max_distance = float(response.ultrasonic_max_dist)
                ros_robot_interface.front_cliff_sensors[i]._field_of_view = response.ir_edge_sens_fov
                ros_robot_interface.front_cliff_sensors[i]._trigger_distance = float(response.ir_edge_sens_range)
                ros_robot_interface.back_cliff_sensors[i]._field_of_view = response.ir_edge_sens_fov
                ros_robot_interface.back_cliff_sensors[i]._trigger_distance = float(response.ir_edge_sens_range)

            return
        self.get_logger().error("Init config vars future result empty!")

    @staticmethod
    def diagnostics_call(msg: DiagnosticStatus) -> None:
        ros_robot_interface._call_diag_recv_safe_ros(msg)

    @staticmethod
    def pico_a_misc_sens_call(msg: MiscSensorsA) -> None:
        timestamp = array.array("L", [msg.time.sec, msg.time.nanosec])
        ros_robot_interface.pico_a_temp._temperature = msg.cpu_temp
        ros_robot_interface.pico_a_temp._last_timestamp = timestamp
        ros_robot_interface.imu_compass._acceleration = array.array("f", [msg.imu_accel.x, msg.imu_accel.y, msg.imu_accel.z])
        ros_robot_interface.imu_compass._gyroscope = array.array("f", [msg.imu_gyro.x, msg.imu_gyro.y, msg.imu_gyro.z])
        ros_robot_interface.imu_compass._compass = array.array("f", [msg.imu_compass.x, msg.imu_compass.y, msg.imu_compass.z])
        ros_robot_interface.imu_compass._temperature = msg.imu_temp
        ros_robot_interface.imu_compass._is_free_fall_triggered = msg.imu_freefall_int
        ros_robot_interface.imu_compass._last_timestamp = timestamp
        ros_robot_interface.imu_compass._call_update_callback_safe()
        ros_robot_interface.pico_a_temp._call_update_callback_safe()

    @staticmethod
    def ultrasonic_sens_call(msg: UltrasonicSensors) -> None:
        timestamp = array.array("L", [msg.time.sec, msg.time.nanosec])
        ros_robot_interface.ultrasonic_sensors[0]._reading = msg.ultrasonic_f_reading
        ros_robot_interface.ultrasonic_sensors[1]._reading = msg.ultrasonic_b_reading
        ros_robot_interface.ultrasonic_sensors[2]._reading = msg.ultrasonic_r_reading
        ros_robot_interface.ultrasonic_sensors[3]._reading = msg.ultrasonic_l_reading

        for i in range(0, 4):
            ros_robot_interface.ultrasonic_sensors[i]._last_timestamp = timestamp
            ros_robot_interface.ultrasonic_sensors[i]._call_update_callback_safe()

    @staticmethod
    def cliff_sens_call(msg: FalloffSensors) -> None:
        timestamp = array.array("L", [msg.time.sec, msg.time.nanosec])

        for i in range(0, 4):
            ros_robot_interface.front_cliff_sensors[i]._is_triggered = msg.ir_edge_sens_front_trig[i]
            ros_robot_interface.front_cliff_sensors[i]._last_timestamp = timestamp
            ros_robot_interface.back_cliff_sensors[i]._is_triggered = msg.ir_edge_sens_back_trig[i]
            ros_robot_interface.back_cliff_sensors[i]._last_timestamp = timestamp
            ros_robot_interface.front_cliff_sensors[i]._call_update_callback_safe()
            ros_robot_interface.back_cliff_sensors[i]._call_update_callback_safe()

    @staticmethod
    def motor_ctrl_state_r_call(msg: MotorCtrlState) -> None:
        ros_robot_interface.right_motor_controller._controller_enabled = msg.controller_enabled
        ros_robot_interface.right_motor_controller._current_pid_out = msg.pid_output
        ros_robot_interface.right_motor_controller._enc_pulse_counts = array.array("l", msg.total_enc_counts)
        ros_robot_interface.right_motor_controller._measured_rpms = array.array("f", msg.measured_rpms)
        ros_robot_interface.right_motor_controller._measured_dirs = list(msg.measured_dirs)
        ros_robot_interface.right_motor_controller._target_rpm = msg.target_rpm
        ros_robot_interface.right_motor_controller._target_dir = msg.target_dir
        ros_robot_interface.right_motor_controller._power_output_voltage = msg.driver_out_voltage
        ros_robot_interface.right_motor_controller._power_current_ma = msg.total_current
        ros_robot_interface.right_motor_controller._last_timestamp = array.array("L", [msg.time.sec, msg.time.nanosec])
        ros_robot_interface.right_motor_controller._call_update_callback_safe()

    @staticmethod
    def motor_ctrl_state_l_call(msg: MotorCtrlState) -> None:
        ros_robot_interface.left_motor_controller._controller_enabled = msg.controller_enabled
        ros_robot_interface.left_motor_controller._current_pid_out = msg.pid_output
        ros_robot_interface.left_motor_controller._enc_pulse_counts = array.array("l", msg.total_enc_counts)
        ros_robot_interface.left_motor_controller._measured_rpms = array.array("f", msg.measured_rpms)
        ros_robot_interface.left_motor_controller._measured_dirs = deepcopy(list(msg.measured_dirs))
        ros_robot_interface.left_motor_controller._target_rpm = msg.target_rpm
        ros_robot_interface.left_motor_controller._target_dir = msg.target_dir
        ros_robot_interface.left_motor_controller._power_output_voltage = msg.driver_out_voltage
        ros_robot_interface.left_motor_controller._power_current_ma = msg.total_current
        ros_robot_interface.left_motor_controller._last_timestamp = array.array("L", [msg.time.sec, msg.time.nanosec])
        ros_robot_interface.left_motor_controller._call_update_callback_safe()

    @staticmethod
    def encoder_odom_call(msg: FastOdometry) -> None:
        ros_robot_interface.encoder_odometry._position = array.array("f", [msg.pose.position.x, msg.pose.position.y, msg.pose.position.z])
        ros_robot_interface.encoder_odometry._linear_accel = array.array("f", [msg.twist.linear.x, msg.twist.linear.y, msg.twist.linear.z])
        ros_robot_interface.encoder_odometry._angular_accel = array.array("f", [msg.twist.angular.x, msg.twist.angular.y, msg.twist.angular.z])
        ros_robot_interface.encoder_odometry._orientation = array.array("f", [msg.pose.orientation.x, msg.pose.orientation.y, msg.pose.orientation.z, msg.pose.orientation.w])
        ros_robot_interface.encoder_odometry._header_frame_id = msg.header.frame_id
        ros_robot_interface.encoder_odometry._child_frame_id = msg.child_frame_id
        ros_robot_interface.encoder_odometry._last_timestamp = array.array("L", [msg.header.stamp.sec, msg.header.stamp.nanosec])
        ros_robot_interface.encoder_odometry._call_update_callback_safe()

    @staticmethod
    def pico_b_misc_sens_call(msg: MiscSensorsB) -> None:
        timestamp = array.array("L", [msg.time.sec, msg.time.nanosec])
        ros_robot_interface.pico_b_temp._temperature = msg.cpu_temp
        ros_robot_interface.pico_b_temp._last_timestamp = timestamp
        ros_robot_interface.fp_switches._switch_1_state = msg.control_mode_switch
        ros_robot_interface.fp_switches._switch_2_state = msg.speed_sel_switch
        ros_robot_interface.fp_switches._last_timestamp = timestamp
        ros_robot_interface.temperature_sensor._temperature = msg.env_temp
        ros_robot_interface.temperature_sensor._humidity_percent = msg.env_humidity
        ros_robot_interface.temperature_sensor._last_timestamp = timestamp
        ros_robot_interface.camera_leds._set_pwm_vals = array.array("i", msg.camera_led_vals)
        ros_robot_interface.camera_leds._last_timestamp = timestamp
        ros_robot_interface.battery._power_current_milliamps = msg.battery_current
        ros_robot_interface.battery._power_voltage = msg.battery_voltage
        ros_robot_interface.battery._last_timestamp = timestamp
        ros_robot_interface.battery._call_update_callback_safe()
        ros_robot_interface.camera_leds._call_update_callback_safe()
        ros_robot_interface.temperature_sensor._call_update_callback_safe()
        ros_robot_interface.fp_switches._call_update_callback_safe()
        ros_robot_interface.pico_b_temp._call_update_callback_safe()

    @staticmethod
    def micro_sw_sens_call(msg: MicroSwSensors) -> None:
        timestamp = array.array("L", [msg.time.sec, msg.time.nanosec])
        ros_robot_interface.micro_switches[0]._is_triggered = msg.micro_fr_trig
        ros_robot_interface.micro_switches[1]._is_triggered = msg.micro_fl_trig
        ros_robot_interface.micro_switches[2]._is_triggered = msg.micro_br_trig
        ros_robot_interface.micro_switches[3]._is_triggered = msg.micro_bl_trig

        for i in range(0, 4):
            ros_robot_interface.micro_switches[i]._last_timestamp = timestamp
            ros_robot_interface.micro_switches[i]._call_update_callback_safe()


# ---- Node object ----
pico_ros_node: RosNode


# ---- Execution ----
def is_ros_node_initialized() -> bool:
    global pico_ros_node
    return isinstance(pico_ros_node, RosNode)

def get_ros_node() -> RosNode:
    global pico_ros_node
    return pico_ros_node
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

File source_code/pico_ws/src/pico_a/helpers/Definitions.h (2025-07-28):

/*
    The ROS robot project - Program Definitions - Pico A
    Copyright 2022-2024 Samyar Sadat Akhavi
    Written by Samyar Sadat Akhavi, 2022-2024.
 
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
    You should have received a copy of the GNU General Public License
    along with this program.  If not, see <https: www.gnu.org/licenses/>.
*/

#pragma once
#include "../../Diagnostics_Names.h"
#include "local_helpers_lib/Common_Definitions.h"
#include "hardware/i2c.h"
#include "Diag_Msgs.h"


// ------- Pin definitions -------

// ---- Misc. ----
#define power_led       1
#define ready_sig       28
#define pi_power_relay  6
#define edge_sens_en    0

// ---- Ultrasonic sensor ----
#define front_ultra_io        13
#define back_ultra_trig_mux   0
#define back_ultra_echo_mux   1
#define right_ultra_trig_mux  2
#define right_ultra_echo_mux  3
#define left_ultra_trig_mux   4
#define left_ultra_echo_mux   5
#define extra_ultra_trig_mux  6
#define extra_ultra_echo_mux  7

// ---- Analog multiplexer ----
#define analog_mux_s0  3
#define analog_mux_s1  2
#define analog_mux_s2  4
#define analog_mux_s3  5
#define analog_mux_io  26

// ---- Motor encoders & motor driver ----
#define l_motor_1_enc_b  12   // Supposed to be 27, temporarily swapped.
#define l_motor_1_enc_a  27   // Supposed to be 12, temporarily swapped.
#define l_motor_2_enc_b  10   // Supposed to be 9, temporarily swapped.
#define l_motor_2_enc_a  9    // Supposed to be 10, temporarily swapped.
#define r_motor_1_enc_b  8
#define r_motor_1_enc_a  7
#define r_motor_2_enc_b  11
#define r_motor_2_enc_a  22
#define l_motor_drive_1  18
#define l_motor_drive_2  19
#define r_motor_drive_1  20
#define r_motor_drive_2  21

// ---- I2C ----
#define i2c_inst  i2c1   // I2C instance (14 & 15 are on I2C1)
#define i2c_sda   14
#define i2c_scl   15


// ------- Other definitions -------

// ---- MicroROS node config ----
#define UROS_NODE_NAME                     "pico_a"
#define UROS_NODE_NAMESPACE                ""
#define UROS_NODE_DOMAIN_ID                95
#define AGENT_WAITING_LED_TOGGLE_DELAY_MS  500   // In milliseconds
#define AGENT_AVAIL_LED_TOGGLE_DELAY_MS    250   // In milliseconds
#define EXECUTOR_EXEC_INTERVAL_MS          75    // In milliseconds
#define EXECUTOR_EXEC_TIME_LIMIT_MS        100   // In milliseconds
#define EXECUTOR_TIMEOUT_MS                20    // In milliseconds

// ---- Repeating timer intervals ----
#define motor_odom_rt_interval          50    // In milliseconds
#define ultra_pub_rt_interval           200   // In milliseconds
#define edge_ir_pub_rt_interval         100   // In milliseconds
#define sensors_pub_rt_interval         500   // In milliseconds
#define motor_enc_method_2_rt_interval  150   // In milliseconds

// ---- Ultrasonic sensor specs ----
#define ultra_fov                    30
#define ultra_min_dist               1         // In cm
#define ultra_max_dist               400       // In cm
#define ultrasonic_signal_timout_us  24*1000   // 24 milliseconds
#define ultra_selftest_measurements  5
#define ultra_selftest_range_min_cm  18        // In cm
#define ultra_selftest_range_max_cm  22        // In cm

// ---- IR edge sensors ----
#define ir_edge_detection_range          3   // In cm
#define ir_edge_fov                      20
#define num_ir_sensors                   8
#define ir_trigger_limit                 2000
#define ir_self_test_z_score_threshhold  2.5f

// ---- Motor controller & safety ----
#define motor_safety_trigger_timeout        3500     // In milliseconds
#define motor_actual_vs_set_extra_timeout   4000     // In milliseconds
#define motor_single_side_max_difference    10       // In RPM
#define motor_set_vs_actual_max_difference  60       // In RPM
#define motor_rpm_method_1_cutoff           18       // In RPM
#define right_motor_controller_id           0
#define left_motor_controller_id            1
#define motor_auto_reverse_cooldown_ms      4*1000   // 4 seconds

// ---- Motor specs ----
#define enc_pulses_per_rot              2
#define gear_ratio_motor                80/1
#define wheel_diameter                  100.0f                  // In millimeters
#define wheelbase                       140.0f                  // In millimeters
#define track_width                     250.0f                  // In millimeters
#define wheel_circumference             (PI * wheel_diameter)   // In millimeters
#define enc_pulses_per_meter_of_travel  (1000 / wheel_circumference) * (gear_ratio_motor * enc_pulses_per_rot)

// ---- Frame IDs ----
#define odom_frame_id       (char *) "odom"
#define base_link_frame_id  (char *) "base_link"

// ---- MPU6050 IMU ----
#define mpu6050_i2c_address            0x68
#define mpu6050_selftest_trim_dev_lim  14
#define mpu6050_gyro_calib_cycles      100

// ---- Misc. ----
#define SETUP_TASK_STACK_DEPTH    1024   // In FreeRTOS words
#define TIMER_TASK_STACK_DEPTH    1024   // In FreeRTOS words
#define GENERIC_TASK_STACK_DEPTH  1024   // In FreeRTOS words
#define STARTUP_WAIT_TIME_S       3      // In seconds

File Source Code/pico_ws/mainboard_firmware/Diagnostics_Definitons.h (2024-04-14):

/*
    The ROS robot project - Common Program Definitions
    Copyright 2022-2024 Samyar Sadat Akhavi
    Written by Samyar Sadat Akhavi, 2022-2024.
 
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
    You should have received a copy of the GNU General Public License
    along with this program.  If not, see <https: www.gnu.org/licenses/>.
*/

#pragma once


// ------- Diagnostics Hardware Names -------
#define DIAG_HWNAME_MOTOR_CTRL_L   (char*) "motor_control_left"
#define DIAG_HWNAME_MOTOR_CTRL_R   (char*) "motor_control_right"
#define DIAG_HWNAME_ULTRASONICS    (char*) "ultrasonic_sensors"
#define DIAG_HWNAME_ENV_SENSORS    (char*) "env_sensors"
#define DIAG_HWNAME_IR_EDGE_FRONT  (char*) "ir_edge_sensors_front"
#define DIAG_HWNAME_IR_EDGE_BACK   (char*) "ir_edge_sensors_back"
#define DIAG_HWNAME_BATT_MON       (char*) "battery_monitoring"
#define DIAG_HWNAME_SYS_PWR_MGMT   (char*) "system_power_management"
#define DIAG_HWNAME_USER_INPUTS    (char*) "user_inputs"
#define DIAG_HWNAME_UCONTROLLERS   (char*) "microcontrollers"
#define DIAG_HWNAME_UROS           (char*) "microros"


// ------- Diagnostics Hardware IDs -------
#define DIAG_HWID_MOTOR_ENC_L1    (char*) "motor_encoder_left_1"
#define DIAG_HWID_MOTOR_ENC_L2    (char*) "motor_encoder_left_2"
#define DIAG_HWID_MOTOR_ENC_R1    (char*) "motor_encoder_right_1"
#define DIAG_HWID_MOTOR_ENC_R2    (char*) "motor_encoder_right_2"
#define DIAG_HWID_MOTOR_DRV_L     (char*) "motor_driver_left"
#define DIAG_HWID_MOTOR_DRV_R     (char*) "motor_driver_right"
#define DIAG_HWID_ULTRASONIC_F    (char*) "ultrasonic_front"
#define DIAG_HWID_ULTRASONIC_B    (char*) "ultrasonic_back"
#define DIAG_HWID_ULTRASONIC_R    (char*) "ultrasonic_right"
#define DIAG_HWID_ULTRASONIC_L    (char*) "ultrasonic_left"
#define DIAG_HWID_ENV_DHT11       (char*) "env_sens_dht11"
#define DIAG_HWID_ENV_IMU         (char*) "env_sens_imu"
#define DIAG_HWID_IR_EDGE_F1      (char*) "ir_edge_front_sens_1"
#define DIAG_HWID_IR_EDGE_F2      (char*) "ir_edge_front_sens_2"
#define DIAG_HWID_IR_EDGE_F3      (char*) "ir_edge_front_sens_3"
#define DIAG_HWID_IR_EDGE_F4      (char*) "ir_edge_front_sens_4"
#define DIAG_HWID_IR_EDGE_B1      (char*) "ir_edge_back_sens_1"
#define DIAG_HWID_IR_EDGE_B2      (char*) "ir_edge_back_sens_2"
#define DIAG_HWID_IR_EDGE_B3      (char*) "ir_edge_back_sens_3"
#define DIAG_HWID_IR_EDGE_B4      (char*) "ir_edge_back_sens_4"
#define DIAG_HWID_IR_EDGE_FADC    (char*) "ir_edge_front_adc"
#define DIAG_HWID_IR_EDGE_BADC    (char*) "ir_edge_back_adc"
#define DIAG_HWID_BATT_PWR_MON    (char*) "batt_power_monitor"
#define DIAG_HWID_BATT_TEMP_MON   (char*) "batt_temp_monitor"
#define DIAG_HWID_SYSPWR_12V_MON  (char*) "sys_power_12v_bus_monitor"
#define DIAG_HWID_SYSPWR_5V_MON   (char*) "sys_power_5v_bus_monitor"
#define DIAG_HWID_SYSPWR_3v3_MON  (char*) "sys_power_3v3_bus_monitor"
#define DIAG_HWID_SYSPWR_12V_REG  (char*) "sys_power_12v_regulator"
#define DIAG_HWID_SYSPWR_5V_REG   (char*) "sys_power_5v_regulator"
#define DIAG_HWID_SYSPWR_3v3_REG  (char*) "sys_power_3v3_regulator"
#define DIAG_HWID_UI_NEXTION      (char*) "user_interface_nextion"
#define DIAG_HWID_MCU_MABO_A      (char*) "mcu_mainboard_rp2040_a"
#define DIAG_HWID_MCU_MABO_B      (char*) "mcu_mainboard_rp2040_b"
#define DIAG_HWID_MCU_POBO        (char*) "mcu_powerboard_rp2040"
#define DIAG_HWID_MCU_MOTBO       (char*) "mcu_motorboard_rp2040"
#define DIAG_HWID_UROS            (char*) "microros"

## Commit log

2022-07-14 CAD Designs complete
    [Back_Screw_Cover.SLDPRT, Back_Screw_Cover.STEP, Back_Screw_Cover.STL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]
2022-08-03 1st draft of circuit diagram, Source code development started
    [Circuit_Diagram.fzz]
2022-08-28 Development continues
    [Circuit_Diagram.fzz]
2022-10-16 PCBs and updated circuit diagram
    [Circuit_Diagram.fzz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]
2022-10-26 Development of motor encoder system continues
2022-11-20 Update schematics
    [ROS Robot main board.PrjPcb, ROS Robot main board.SchDoc]
2022-11-22 Circuit diagram update
    [Circuit_Diagram.fzz]
2022-11-26 Structure Change
    [Circuit_Diagram.fzz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]
2022-12-12 Update improvements list for CAD
2023-05-26 Multiple updates, encoder testing, ignore Pico code.
    [Circuit_Diagram.fzz, ROS Robot main board.PrjPcb]
2023-05-26 Schematics update
    [ROS Robot main board.SchDoc]
2023-05-26 Schematic update
    [ROS Robot main board.PrjPcb]
2023-08-21 Source code update - Encoders now work
2023-08-24 Motor PID control now works.
2023-08-24 Started work on motor control library.
2023-09-10 Motor Control library development continues...
2023-10-04 Motor direction control added.
2023-12-06 Motor library almost finished.
2023-12-07 Motor_lib test program
2023-12-14 Motor_lib testing started, Motor_lib bugfixes.
2023-12-22 Motor_lib testing completed.
2023-12-22 Motor.c++ comments finished.
2023-12-23 Motor_lib comments almost finished. Minor improvements to the MotorSafety module of Motor_lib.
2023-12-25 Motor_lib completed.
2024-01-07 Raspberry Pi Pico firmware development continues...
2024-01-07 Overall circuit diagram update
    [Circuit_Diagram.fzz]
2024-02-24 Raspberry Pi Pico firmware dev continues.
    [Main_Board.PrjPcb]
2024-03-06 File structure re-org, Docker, prep for custom uros msgs.
    [Back_Screw_Cover.SLDPRT, Back_Screw_Cover.STEP, Back_Screw_Cover.STL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]
2024-03-06 Folder structure re-org
    [Back_Screw_Cover.SLDPRT, Back_Screw_Cover.STEP, Back_Screw_Cover.STL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]
2024-03-17 New V2 wheel with integrated shaft converter.
    [Back_Screw_Cover.SLDPRT, Green_led.SLDPRT, HY_SRF_05.SLDPRT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]
2024-04-07 Raspberry Pi Pico Firmware build config completed.
2024-04-12 Sensor publishing work continues...
2024-04-14 Pico A Firmware Almost Complete
2024-04-15 Pico A firmware ready for testing. Logging is TODO.
2024-04-16 Pico A & Pico B firmware ready for testing.
    [Circuit_Diagram.fzz]
2024-04-16 Update PID library.
2024-04-28 Library structure re-org, Devcontainer updates, write_log() over UART now works.
2024-04-30 Devcontainer updates (GUI support, Nvidia GPU resources, Debug Probe now works properly, Pico TTY permissions fixed), testing and debugging continues.
    [Definitions.h]
2024-06-17 Added Pico build workflow.
2024-06-17 Fix Pico SDK import.
2024-06-19 Run CodeQL in the same container as Pico build.
2024-06-20 Removed binary pico builds.
2024-06-20 Updated PID lib and pico_ws README.
2024-07-04 Pico A firmware tested and almost ready. Self-test, PID autotune, and IMU auto-calib remaining.
2024-07-08 Added IR edge and ultrasonic self-tests to Pico A.
2024-07-08 Pico A & Pico B firmware completed. 1 bug remaining; affects both picos.
    [Definitions.h, Diag_Msgs.h]
2024-07-08 Pico B include cleanup.
2024-07-13 Raspberry Pi Pico firmware completed and tested.
2024-07-22 Pico firmware bugfixes & updates.
    [Definitions.h]
2024-07-24 Remove unused variable from Motor_Safety.c++.
2024-08-25 Created python robot driver and ROS wrapper for driver.
2024-08-25 Added "_deps" directory to ignore list for Pico build action.
2024-08-25 Changed Pico SDK branch to "1.5.1" for Pico workspace devcontainer.
2024-08-28 Update settings & Pico Libraries.
2024-09-09 Robot driver wrapper update.
2024-10-04 Minor firmware and Python driver fix.
2024-10-06 Minor pico firmware & driver updates/fixes.
    [ros_main.py]
2024-11-07 Submodule updates & repo re-structure.
    [Assembly.SLDASM, Back_Screw_Cover.SLDPRT, Back_Screw_Cover.STEP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]
2024-11-08 Updated some directory names.
    [Green_led.SLDPRT, HY_SRF_05.SLDPRT, L298N_driver_board.SLDPRT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]
2024-12-15 Odometry computation formula fixes and cliff sensor calibration function fix.
    Note: temporarily disabled ultrasonic sensors, awaiting optimisations.
    [Definitions.h]
2024-12-23 Added launch descriptions for robot driver, started working on Docker container for deploying on Raspberry Pi 5.
2024-12-25 Finished work on Docker container for deploying robot driver on to Raspberry Pi 5.
2025-01-22 Added camera_ros package for publishing Raspberry Pi Camera images.
2025-06-12 More work on bringup, new Collada 3D models for robot description. Bringup incomplete, work in progress.
    [15x30_Blank_PCB.SLDPRT, Assembly.SLDASM, Back_Screw_Cover.SLDPRT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]
2025-07-24 Added robot description package.
    [body.xacro, camera_led.xacro, gazebo.xacro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]
2025-07-27 Robot description fixes, many new infra packages added. Ready for Nav2.
    [body.xacro, camera_led.xacro, common_macros.xacro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]
2025-07-28 Various fixes, driver namespace issue resolved.
    [Definitions.h, ros_main.py]
2025-07-28 Driver fix.
2025-07-28 Temporary driver hotfix.
2025-07-28 Re-publish using current ROS clock.
2025-07-29 Camera launch fixes.
2025-07-29 Camera calibration added, various fixes.
    [camera_calib.yaml]
2025-07-29 Fixed camera config and calib.
    [camera_calib.yaml]
2025-07-29 Camera orientation fix.
    [rpi_camera.xacro]
2025-07-29 Camera orientation fix #2
    [rpi_camera.xacro]
2025-07-29 Camera orientation fix #3
    [rpi_camera.xacro]
2025-07-30 Fixed camera (optical) orientation.
    [body.xacro, camera_calib.yaml, rpi_camera.xacro]
2025-07-30 Fix camera flip.
    [rpi_camera.xacro]
2025-07-30 Fixed sensor frame ids.
    [interface_callbacks.py]
2025-07-30 Fixed wheel rotation axis.
    [body.xacro, wheel.xacro]
2025-07-30 Fix wheel rotation direction.
    [wheel.xacro]
2025-07-30 RPLiDAR config changes.
    [body.xacro]
2025-07-30 Updated RViz config and lidar position.
    [body.xacro]
2025-08-30 New wheel design (again), added navigation package. Still WIP.
    [Wheel_V2_Flat.SLDPRT, Wheel_V2_Flat.STEP, Wheel_V2_Flat.STL]
2025-09-07 Driver namespace hotfix, twist mux remap fix.
2025-09-09 New calibration coefficients for odometry.

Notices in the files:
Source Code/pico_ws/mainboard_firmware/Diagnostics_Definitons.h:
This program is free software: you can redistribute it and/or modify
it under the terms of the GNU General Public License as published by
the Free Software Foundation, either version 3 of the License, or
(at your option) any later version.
